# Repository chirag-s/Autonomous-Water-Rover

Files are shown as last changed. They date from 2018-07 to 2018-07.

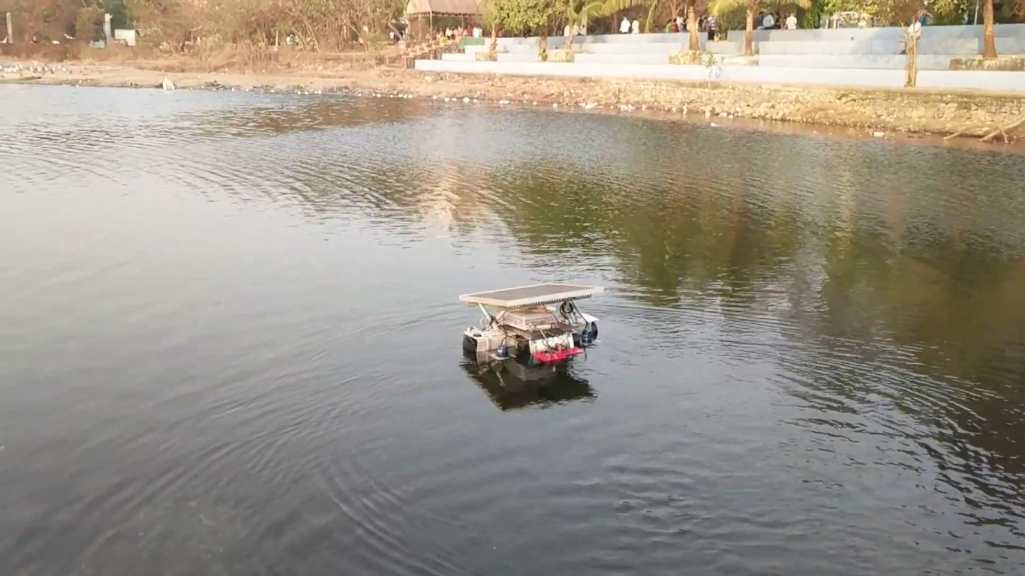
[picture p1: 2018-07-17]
Project Images/Project Testing/Mini Seasoe Testing manual.png

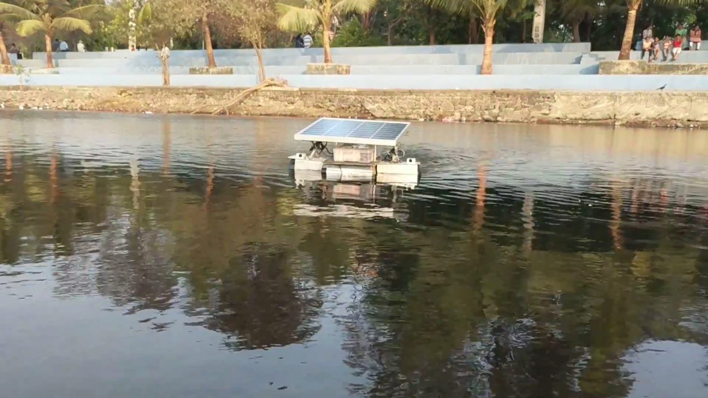
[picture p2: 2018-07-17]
Project Images/Project Testing/Mini seashore testing .png

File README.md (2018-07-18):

# Autonomous-Water-Rover

Water pollution is an age-old problem. Effective technologies and regulations to counter this is still under research with a booming rate. However, to solve a problem, identification and localization of the root source is essential. Today, to recognize the lakes or any other water bodies not satisfying the safety regulation, manual methods are employed. Stationary ground stations with sensors immersed at fixed points are used to measure the water parameters.

The Autonomous Water Rover monitors a water body by following the path specified by the user using GPS coordinates and traverses the water body as per the instructions with obstacle avoidance. It has different sensors like pH, percentage of dissolved oxygen, temperature, turbidity, etc. which gives us real time data on our server about the different parameters of the water body. A sonar transducer is also used to provide depth information up to 100 feet. The depth information of a water body can be used by ports, dredging companies and hydrographic offices. The rover also has a camera with first person view which can stream live video to a website in case of any emergencies regarding the waters or on rover itself. An AWR is really helpful as it will autonomously do some specified tasks which at present are carried out by humans.

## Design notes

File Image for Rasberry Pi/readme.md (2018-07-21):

The Configured Image for the Raspberry Pi is available on the below link :-

https://drive.google.com/file/d/1N4698NO5Q2EfMxIUc71g-TSj_-oGwf1t/view?usp=sharing

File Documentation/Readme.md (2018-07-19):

AWR Circuit Diagram
--|Contains the schematic used for motor driver, power distribution and arduino pro mini shield

Circuit Image
--|Shows the assembled circuit to give a gist regarding the wiring

Final Thesis Submission
--|Explains the entire project in great detail

Hardware Setup Guide
--|Explains the system components and the circuit diagram

Mechanical Setup Guide
--|Explains the mechanical assembly in DIY format

Process Flow
--|It expalins the steps the user has to follow with an Autonomous Water Rover to make it work through a flow chart
Software Setup Guide
--|Explains the software requirements and useful links to debug errors while setting up this project.
--|The codes folder in the repository has the entire file structure and its explanation.

Under Water Image Processing
--|It contains the explanation to the processing done, for under water images captured using a GoPro

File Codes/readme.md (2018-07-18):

File Structure

Arduino RC to PWM
--> Code to be uploaded on arduino used for reading Rc outputs from navio 2

Arduino Pro Mini
--> Code to be uploaded on arduino used for reading sensor data

SensorLog.py
--> Code to be executed on Raspberry pi having navio2 to get data from arduino having sensors

sensorsData.db
--> Sqlite3 database having two tables
----|GPS Data
-------> Table having only 1 row and is updated by GPS.py in folder WebServer. It stores the lat-lon values along with fix status
----|Sensor Data
-------> Table having sensor data and timestamp

WebServer
--|app.py
----> Execute to start web server
--|static
----> Contains all media, CSS and JS libraries
--|templates
----> Contains all HTML layouts
--| navio
----> Contains libraries necessary in app.py to send RC outputs

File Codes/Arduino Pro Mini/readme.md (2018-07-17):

This file is used for arduino which is used to get sensor data aand send it to RPi

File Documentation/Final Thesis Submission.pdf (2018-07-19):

Chapter 1: Introduction

This chapter presents the motivation for undertaking this project. It also emphasises the

need of water quality monitoring and our objectives.

### 1.1 Motivation

At present, in India, lakes and wetlands are in varying degrees of environmental

degradation due to industrial pollution. Despite knowing their environmental, social and

economic significance, city planners have neglected these water bodies. Today these

water bodies are at a high risk due to sewage and garbage disposal.

Pollution in large water bodies has resulted in a lot of disasters affecting aquatic life and

the complete biocoenosis. Carcasses of aquatic animals are washed off shore due to

mixing of pollutants, oil spills, etc. Thus, we felt a need to monitor the health of such

large water bodies, using sensors and GPS control, in order to maintain balance in the

ecosystem.

After a discussion about our project with an Indian Navy officer at INMEX SMM 2017

we realised about the problems faced by port authorities, to maintain channel depth to

prevent grounding of ships. In most ports, channel depth is identified separately by a

coast guard. However, this can be done by a rover which can use SONAR and model the

underwater bed of waterways so that we can keep a track and maintain a pathway for

boats.

Flooding of cities and villages happens due to various reasons. On 29th August, 2017

Mumbai was flooded. In the aftermath, it came to light that a doctor lost his life because

of an open manhole. We believe that in the aftermath of floods, our autonomous rover

will be capable of detecting such manholes via SONAR and pave a road where it is safe

to walk. Also, emergency supplies like medical aid/food can also be delivered to stranded

people at required locations using the rover by rescue officials.

After speaking to scientists at National Institute of Oceanography, Goa we understood

that underwater imaging is required to study the geological features of the coast.

Traditional surveillance boats cannot be operated in these shallow waters hence the

Autonomous Water Rover can be used to get underwater images in these regions.

The following articles published in leading newspapers emphasize on the water quality

problems observed in India :

Fig. 1.1 Water Pollution in 2018 | Fig. 1.2 Water Pollution in 2016

From above two articles it can be seen that the pollution in Powai lake has increased 1.6

times in just two years and if active measures are not taken to curb pollution it will likely

increase in the coming years.

### 1.2 Objective

The Autonomous Water Rover (AWR) is aimed to be an unmanned surface vehicle that is capable of traversing water bodies in remote controlled or in autonomous mode.

The AWSR is aimed to be developed as a novel marine monitoring and surveillance technology that can continuously collect data on water quality in lakes, rivers, channels, ports and estuaries. The water parameters targeted are pH, temperature, turbidity, salinity and depth. The list of parameters were finalised after interaction with scientists from Naval Materials Research Laboratory and National Institute of Oceanography.

The AWSR will traverse a water body by following the path specified by the user using GPS coordinates along with active obstacle avoidance. It will also have a manual mode accessible through a website.

It will have surveillance equipment in the form of waterproof camera for underwater imaging, a sonar which will illustrate depth contours, fish targets and other structures. These features are of utmost importance for defence and hydrography purposes.

Our aim to track pollution by using Autonomous Water Rover will take the aquatic surveying industry closer to industry 4.0 by incorporating Internet of Things, Robotics and Cloud Computing along other cutting edge technologies. The next chapter summarises research done on unmanned surface vessels for various applications.

Chapter 2: Literature Survey

This chapter presents the overview of the technological research and advancements and the comparative study of various USV technologies and products available commercially along with their applications in research and bathymetry studies.

Papers from 1994 are taken into consideration for this project. Some of the papers were

used to understand autonomous vehicles and their functioning along with applications,

while some were on combined works in all the 3 fields. The research work on all the

fields mentioned above is given below.

### 2.1 Autonomous water vehicles and applications

Exploring water bodies using manned and unmanned vehicles dates back to post WWII.

Since then many developments have been made, which can be broadly classified as

Remote-controlled vehicles and autonomous vehicles.

Some papers have aimed at collecting data from bottom transecting vehicles (ROVER)

[1], while some provide robust designs for research in cooperative autonomy [2]. Rest of

the papers focused on developing different methodology for achieving specified targeted

goals.

Sr. No. | Category | Author(s) | Year
1 | Unmanned Surface Vehicles [3] | Justin E. Manley | 2008
2 | Research | J. Curcio, J. Leonard, A. Patrikalakis | 2014
| | Erion Plaku, James McMahon | 2016
| | Geoffrey A. Hollinger, Urbashi Mitra, and Gaurav S. Sukhatme | 2012
3 | Other Applications | Inspection | Pere Ridao, Marc Carreras, David Ribas, and Rafael Garcia | 2010

| Brian Bingham, Brendan Foley, Hanumant Singh, and Richard Camilli | 2010
| Thomas Birtchnella & Chris Gibsona | 2015
Defense | Thomas Pastore, Vladimir Djapic [4] | 2010
| P.E Hagen, N Storkersen | 2003
| Liam Paull, Sajad Saeedi, Mae Seto | 2012
| E Bovio, D. Cecchi, F. Baralli | 2006

Table 2.1 : List of papers based on applications

### 2.2 Combined study

While few researchers were studying about aquatic life, developments were made

simultaneously in existing models by other engineers and researchers, which involved

combining concepts of machine vision, AI or IP or by satellite control. Their research

works are listed in the table below.

Sr. No. | Category | Author(s) | Year | Specification
1 | Surface Monitorin g and sampling | Goudey, T Consi J. Manley, MGraham | 1998 | Fish Monitoring
| | Caccia M, Bono R, Bruzzone Ga | 2005 | Sea Surface sampling
| | J.E Manley | 1997 | Surface robot
| | J. E. Manley, A. Marsh, W. Cornforth | 2000 | Surface craft
| | Iuliu Vasilescu, Keith Kotay | 2005 | Data collection
| | Matthew Dunbabin, Alistair Grinham, James Udy | 2009 | Surface monitoring

2 | Fish Monitorin g | M Dunbabin, L Marques | 2012 | Monitoring
| | P. Newman | 2002 | Operating Suite
| | J. Vaganay, J. Leonard, J. Curcio, and S. Willcox | 2004 | Navigation
| | Elgar Desa, R. Madhan and P. Maurya | 2006 | Ocean Data
| | Yun-Heh Chen-Burger , Gayathri Nadarajan, Robert B. Fisher | 1995 | Tracking Fish
3 | Depth and bed surface monitorin g | T Vaneck, M Schmidt | 1996 | Bathymetry
| | L. L. Whitcomb, D. R. Yoerger, and H. Singh | 1999 | Navigation of underwater vehicle
| | C.C. Eriksen, (http://ieeexplore.ieee.org/search/searchresult.jsp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) T.J. Osse, (http://ieeexplore.ieee.org/search/searchresult.jsp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) R.D. Light (http://ieeexplore.ieee.org/search/searchresult.jsp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) | 2001 | Depth monitoring and research

Table 2.2 : List of papers based on combined applications

### 2.3 RESEARCH GAP

In all, 23 research papers were studied. These papers were categorized according to the

categories mentioned above. Above literature review shows that studies are going on

simultaneously on autonomous water vehicles as well as their advancement. Thus,

selecting a proper research gap has become an important in this case. A small summary

was made in order to identify the research gap as shown below.

### 2.3.1 Area of Research

In this section, all the papers are broadly classified as per the major area of research.

Main | categories | are: | Research, | Monitoring | and | Defense.

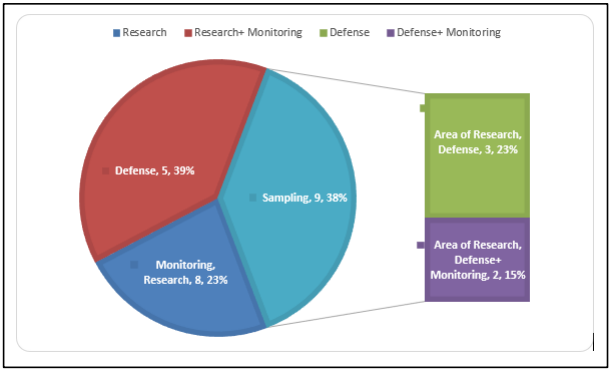
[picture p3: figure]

Fig 2.1 Application based categorisation of literature

From the above chart, it is clear that till date, surface water vehicles are used for data

acquisition mostly targeted on water beds. Least research is in field of dredging and

surface quality monitoring. Hence these field are chosen.

### 2.3.2 Year of Research

Fig

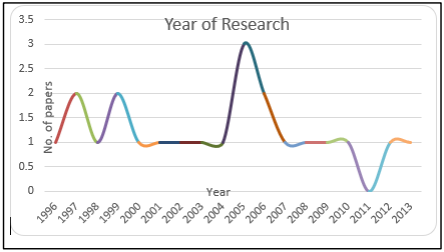
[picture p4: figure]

2.2 Categorisation of literature with time

The above chart shows that research is continuously going on from year 2010 in these

fields. Thus, there is no saturation in our area of research and there is continuous

development in this stream.

### 2.4 A review on water quality mapping in Powai lake

The paper ―Water Quality in Powai Lake, J.G Kiloyar, N.S Rokade, Taal2007: presented

at the 12th World Lake Conference, 2008‖ discusses the water quality of Powai lake

which is a large artificial lake, situated in a northern suburb of Mumbai. The purpose of

this paper, in this survey is to collect information concerning use and value of water

quality monitoring at Powai lake that might affect aquatic life. This paper studies the

changes in different parameters of water as the season changes. For this, it maps the

presence of impurities in the lake and many different parameters like DO, COD,

Nitrogen, TDS, COnducting, Salinity, Chloride, Total Hardness, pH and Alkalinity.

It was observed that during the month wise sampling of the various physio-chemical

parameters of the lake, the samples collected were position specific. However, the

process of collecting the sample was manual and the positional accuracy might have varied over the months. Also, a more precise and accurate data variation can be structured

if the number of samples obtained are more.

The graphs below show the variations of conductivity and pH as measured every month

at six stations over a period of six months.

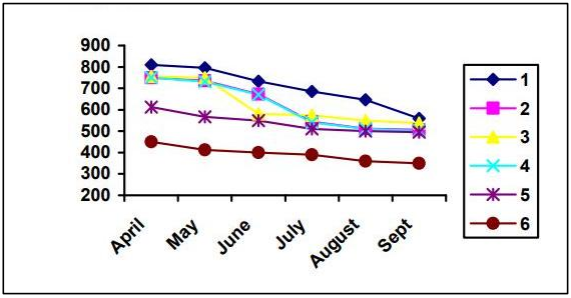
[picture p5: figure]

Fig 2.3 Variation of conductivity with time and location

Fig 2.4 Variation of pH with time and location

### 2.5 Commercially available Unmanned Surface Vehicles

Commercial products were also studied to analyse the existing technologies and the

capital associated to address these problems.

Kongsberg Gruppen located in Norway, has developed GeoSwath 4R USV, for bathymetry and hydrography surveying. It is capable of :
- Ultra high resolution wide swath bathymetry (FOV 240 - degrees)
- Geo-referenced side scan
- Radio control up to a range of 2 km
- Enduring 2.5 hours of continuous operation

Oceanalpha Company Limited located in Guangdong, China has developed ESM30 USV, for water quality monitoring and sampling. It is capable of :

- Measuring parameters such as pH, DO, temperature, ORP, conductivity and turbidity.
- Sampling water at four locations for further analysis in labs.
- Autonomous navigation, remote operation along with obstacle avoidance.
- Video streaming upto 2 km and data communication upto 5 km
- Enduring 3.5 hours of continuous operation
- Cost $52,000/-

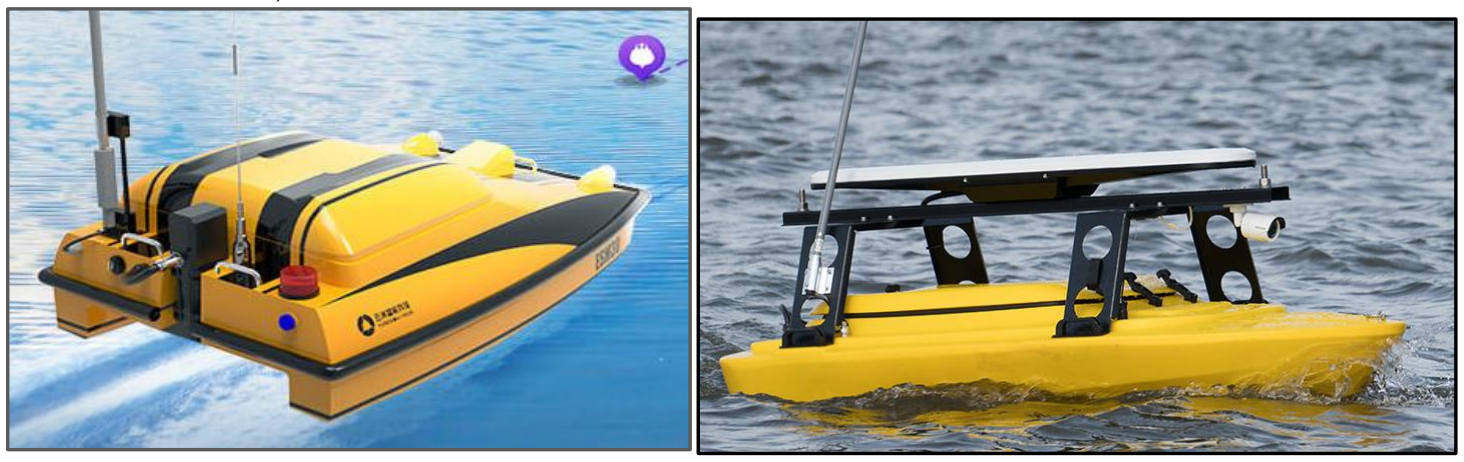
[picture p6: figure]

Fig 2.5 GeoSwath 4R USV | Fig 2.6 ESM30 USV

After going through the ongoing research and development in the field of unmanned

surface vessels, the design and development of Autonomous Water Rover will be

explained in the next chapter.

Chapter 3: Project Design

### 3.1 Design Considerations

The requirement of the surface vehicle with the targeted objectives was the first

consideration for selecting the base of the rover. The rover is required to provide

maximum payload capacity in minimum volume. There should be a container inside or

on the rover which can contain the electronic components for the entire rover. The

compartment must be waterproof and must prevent water from entering the container.

Also while providing with waterproofing the compartment should also not interfere with

any signals that is being transmitted or received by the transceivers inside the

compartment like GPS and compass. A camera is required for first person view of the

rover which should have sufficient field of vision to cover the entire forward path. In

addition the rover should also feature a propulsion system to drive the rover and a

maneuvering system for controlling the heading direction. Additionally, to increase the

mission duration of the rover, it should be provided with a secondary power source

preferably solar power.

### 3.2 Support Structure

3.2.1 Hull selection

After considering our application it became evident that speed was not of great

importance for our use and emphasis was given to simplify the manufacturing process

and keep our project cost-effective. Most boats feature a hull made of aluminium, while

most of the unmanned vehicles tend to feature fiber reinforced polymers. Analysis for

selection of the material of the rover‘s hull was done with feasibility and time as the

major decisive parameters.

Hull material options:

Metal: Most rovers and made with metal hulls. They generally fall in two

categories: Aluminium and Steel. Metal hulls provide high strength and more impact

damage resistance. Relative to their weight, aluminium provide incredible strength and

are highly ductile. The pitfall with metal hulls in water rovers are their vulnerability to

corrosion, scaling and providing shielding effect for components placed inside the hull.

The aluminium hulls are also prone to galvanic corrosion with a stainless steel propeller

or bolts. The outside of the hull are prone to rusting and pitting due to this galvanic

corrosion.

Wood: Wood is another known material which is known to be used for building

boats for a very long time. Wood has less density than water so it floats giving high

buoyancy posing as a safe and sturdy vessel. However, using wood as hull also has some

drawbacks. If left in water for long time, worms eat away the timber. Termites attack the

dry wood. SInce the rover is meant to be used to still waters marine bores poses as a great

threat to the hull. Wood hulls are susceptible to to electrolysis damage. Electrolysis can

cause damage to the to the wood and turn them into mulch and mush.

Fiberglass: Fiberglass reinforced plastics is the most widely used hull material in

unmanned surface as well as underwater vehicles. FIberglass provide thinner hulls with

comparable strength. Thinner hulls do then to flex more and can be given any desired shape. Fiberglass vessels also tend to be lighter and provide sufficient strength for long

lasting structures. Fiberglass are invulnerable to any kind of electrolytic damage or

corrosion. At first glance it seems like fiberglass can be the best available material for the

hull of the rover. The only constraint with it is the availability and the capital required for

its manufacturing.

After examining the available materials and resources we decided to use PVC pipes for

the the support structure for our AWR. The overall benefit of using PVC pipes are:

improved stability, increase in the load capacity and reduction in manufacturing cost.

PVC pipes were used for the following reasons :

- They are manufactured to transport liquids (mostly water); for this they are

manufactured so as to sustain high pressure. The water at the surface of water

bodies exert significantly lesser pressure, making our rover apparently leak

proof.

- Sealing the ends of the pipe is possible as standard end caps are available.
- Multiple pipes can be attached according to the requirement of length and

width in accordance with maximum roll and pitch the rover needs to sustain.

- Impervious to attack from fungi.

While PVC pipes exhibit high resistance to abrasion, they are affected by the

environment. The following are the effects of varying environmental features on the PVC

pipes:

Thermal Effects:

The properties of the PVC pipes are significantly related to the operating

temperatures. The rover must be deployable in wide varieties of water bodies with

varying temperatures. Also the temperature significantly varies throughout the day in a

single water body. PVC pipes are rated for maximum performance at 23°C; as the

operating temperature decreases, the pipe‘s stiffness and the tensile strength increase,

thereby increasing the pipe‘s pressure capacity.

Biological Attack:

PVC pipes are nearly impervious to biological effects. These attacks can be

caused by the action of living microorganisms viz. Bacteria and fungi. PVC pipes will not

deteriorate or break down under such attack, nor will it serve as a nutrient to

microorganisms, or fungi.

Weathering Resistance:

PVC pipes can incur surface damage when subjected to long exposure to

ultraviolet radiation from sunlight. While the rover is supposed to work in direct sunlight

it became imperative to rule out the vulnerability. This was achieved by physical coating

of the pipes with layers of oil paint. Since the ultraviolet degradation occurs when energy

from UV rays leads to excitation of the molecular bonds in the plastic, the layer of paint

prevents any direct contact between the PVC and sunlight.

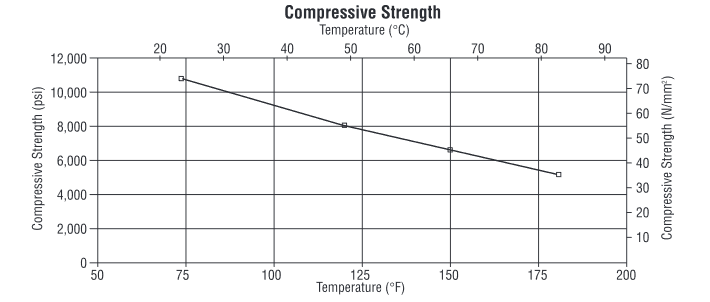
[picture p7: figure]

Fig 3.1 Compressive strength graph for PVC

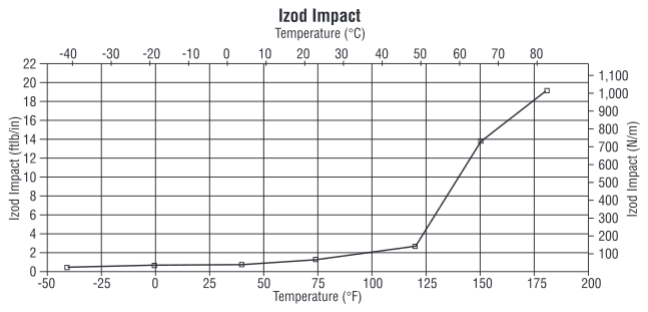
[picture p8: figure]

Fig 3.2 Izod Impact test graph for PVC

### 3.3 Boat Structure:

The primary requirement of the support structure of the rover is to provide stability,

buoyancy and a solid platform. Owing to the limited manufacturability of the PVC pipes,

we selected the conventional raft type structure.

We selected PVC pipes of varying lengths with outer diameter 16 cm and coupled them

together representing a raft for making the support structure of the rover. The middle pipe

was kept the longest and one small pipe was attached on front and back each. This

provided with maximum roll stability while keeping the weight minimum.

The total number of pipes to be joined was decided as per the payload of the rover. The

layer was made by adding 3 pipes of lengths 300 mm, 300 mm and 900 mm.

The three pipes are held together in place using a aluminium strip loop wound around

them. The Al strip is kept in tension to retain its shape and an adhesive is used to close

the loop while retaining it on the pipe. Additionally copper wires were used to increase

the tension in the strip to ensure firm structure of the support.

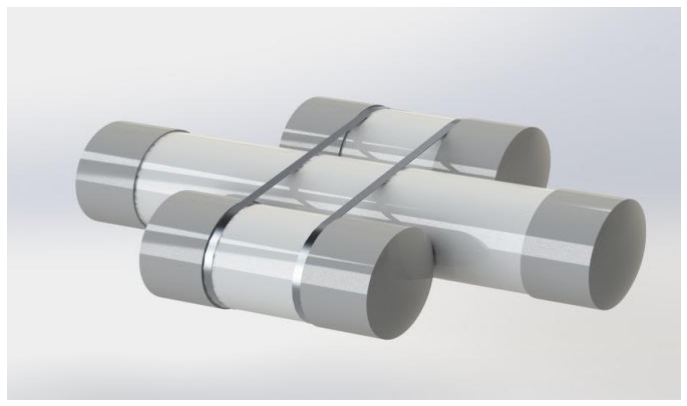
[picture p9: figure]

Fig 3.3 Support Structure

### 3.4 Buoyancy calculation:

Buoyancy = Weight of fluid displaced

Buoyant force is given by:

Volume of pipes :

The total weight of fluid displaced is about 30.56 kg.

### 3.5 Top Plate: The PVC pipes provides round surface which cannot be used for any kind

of mountings. Furthermore to secure waterproofing it was opted to avoid any kind of

drilling in the pipes. So a 2 mm aluminium sheet was used as the top plate to provide a

constant surface. This allowed all the components, equipments and thrusters to be

mounted on the rover with additional reinforcements.

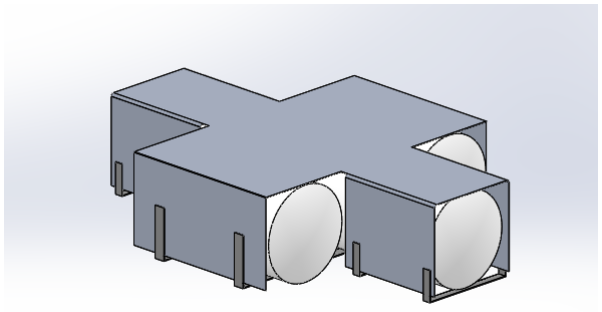
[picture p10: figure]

Fig 3.4 Reinforcements

### 3.6 Propulsion System:

Motor Selection:

The target waters for AWR are still and weedy waters. Conventional propulsion

system has a potential to clog in weeds and needs to be cleared. Instead it was decided to

use differential reaction drive for propulsion using two submersible pumps.

The reaction drive works by having an intake which is located below the hull submerged

in water. Water enters the pump through the inlet. The pump is usually centrifugal pump

for higher speeds or axial flow type for medium or low speeds. The water pressure in

increased inside the pump and is directed outward through a nozzle.

### 3.7 Thrust Calculation:

Thrust from a propeller is given substituting Bernoulli‘s equation into thrust equation

(momentum equation)

Substituting in Bernoulli‘s equation:

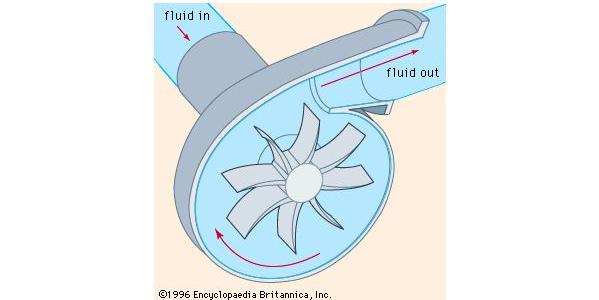
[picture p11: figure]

Fig 3.5 Working of Bilge Pump

The pump selected was Vetus V1000.

The bilge pump exhibits the following superiorities which made it most viable propulsion

system for our rover:

- The bilge pumps are submersible water pumps. So there was no need of

waterproofing the motors.

- Since the impeller is directly attached to the motor shaft in the pump there was no

need for transmission shaft.

- The pumps can be directly mounted outside and there‘s no need to locate them

inside the rover body.

- A filter is provided to prevent seaweed from getting stuck in the impeller.
- Speed can be adjusted by controlling the rotation speed of the motor.

### 3.8 Final Design:

Fig 3.7 CAD of Final Design

The final design includes a polypropylene sheet on top of the aluminium sheet for

insulation from circuits. A solar panel is added to recharge the battery and add to the run

time of the rover.

Principal axes of inertia and principal moments of inertia: ( grams * square millimeters )

Taken at the center of mass.

Ix = ( 0.00, 0.00, 1.00) | Px = 897234608.07
Iy = ( 0.96, 0.27, 0.00) | Py = 1136627042.03
Iz = (-0.27, 0.96, 0.00) | Pz = 1291193297.90

Center of mass: ( millimeters )

X = 2.38

Y = 171.37

Z = 349.05

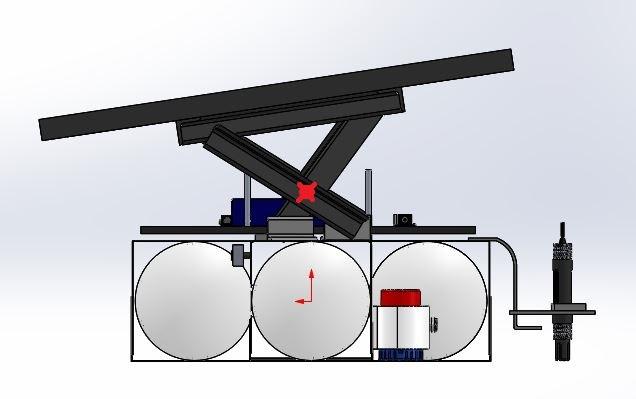
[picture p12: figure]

Fig 3.8 Center of mass position (Side View)

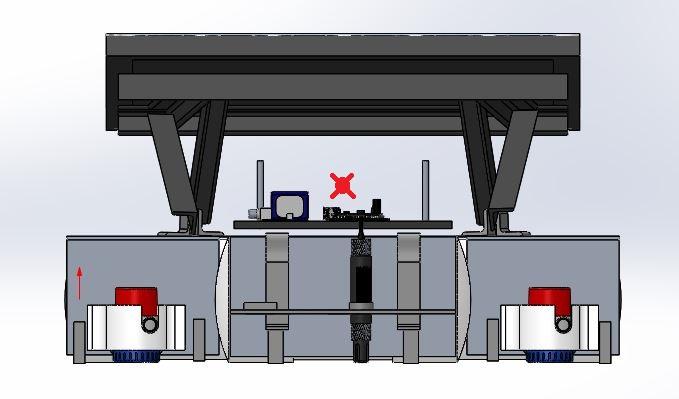
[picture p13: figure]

Fig 3.9 Center of mass position (Rear View)

Chapter 4 : Implementation Details

This chapter presents the hardware design, software implementation, cost report and

testing results for the various components of the Autonomous Water Rover. It also

presents the image processing algorithm used for enhancement of underwater video feed.

### 4.1 System design

The figure below illustrates the various components in the Autonomous Water Rover and

their relation with one another. Some of the components like the thrusters and the solar

panel were explained in the product design section. The hardware and software

components will be covered in this chapter.

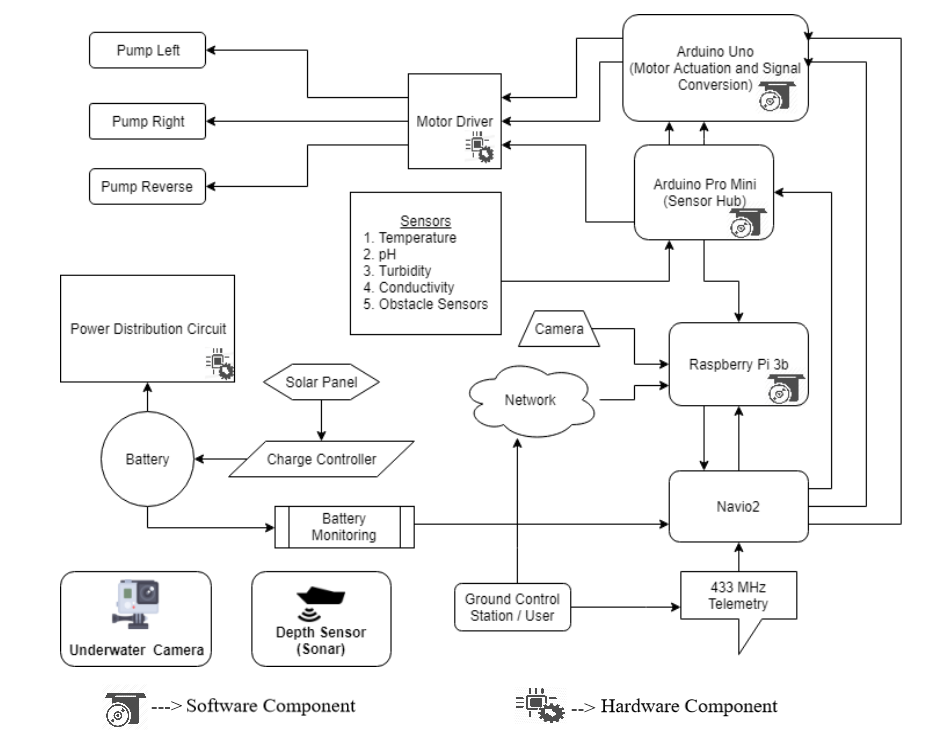
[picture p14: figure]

Fig 4.1 System Design

The various components in the above figure are as follows :-

- Power System: The power generation, storage and distribution includes the

following main components :

- Battery : LiPo will be used to ensure operation of rover for over an hour

on one charging

- Solar Panel : A 50W Solar Panel is used to charge the 12 volt battery and

also increase the operation period

- Charge Controller : A 20A 12V waterproof solar panel charge controller

will be used

- Voltage regulation : Voltage regulators will be used to always keep the

supply voltage for the pumps constant i.e. 12V to obtain similar

performance even at different battery levels. Also 5V and 3.3V voltage

regulators will be used for obtaining required supply voltage for the Rpi

controller board, Navio2, telemetry and all installed sensors on the rover

- Raspberry Pi 3b : It is a single board computer which will be used for complex

path planning through ardupilot, hosting the web interface, providing live video

streaming and communicating with sensor nodes

- Navio2 : It is an autopilot Hat for Raspberry Pi 3b which simplifies autonomous

navigation by bringing multiple sensors on a single board and by seamless

integration with Raspberry Pi. It also has analog to digital converters along with

pulse generators to produce pulses which can control servo motors. The following

sensors will be used by the Autonomous Water Surveillance Rover :

- GNSS Receiver : Tracks GPS, GLONASS, Beidou, Galileo and SBAS

satellites for accurate positioning

- Dual IMU : Accelerometers, gyroscope and magnetometer readings will

be used for orientation and motion sensing

- High resolution barometer : Senses altitude with 10 cm resolution and can

be used to relay accurate location information along with GPS

- Communication Ports : UART interface will be used to relay information

through telemetry radio

- Ground Control Station : It could be any windows based personal computer

having Mission Planner installed

- Local Area Network : A LAN is created to access the website hosted on the

raspberry pi. It is not needed for operation in autonomous mode

- | Telemetry Radio : The | mRo SiK Telemetry Radio V2 operates at 433Mhz and

provides 300m range by default. This radio will be the link to relay localization

details and program missions for the rover remotely

- Underwater Camera : A GoPro hero is used to gather images of the underwater

bed upto three meters. As penetration of light at this depth is sufficient, an

illuminating light source will not be necessary. The light source can be fitted to

the base of the rover for illumination if surveillance is to be done in the absence of

| sunlight
- Camera : A raspberry pi camera version 2 is used to provide live first person

view of the rover to operator

- Sensor Node : Data acquisition from the environment will carried out and the

information will be relayed to the Rpi. An arduino pro mini is used because of its

small form factor for interfacing the sensors and communicating with raspberry pi

- Distance Sensors : Two waterproof ultrasound (40 KHz) distance sensors i.e.

JSN-SR04T are used to detect obstacles on the surface of the water and in the

| forward path of the rover
- Water Quality Monitoring Sensors : To measure the quality of water following

parameters are being measured :-

- pH : DFRobot Gravity : analog pH sensor is being used to measure the pH

of water. The pH measurements have a resolution of ± 0.1pH at 25 ℃

- Temperature : DS18B20 waterproof temperature sensor probe is used to

get ±0.5°C accuracy in the range -10°C to +85°C. It uses 1-Wire interface

i.e. requires only one digital pin for communication

- Conductivity : A generic rain sensitive sensor module is used in analog

mode to get the conductivity readings. The accuracy of this module for

measuring isn‘t high but can be used for thresholding purposes

- Turbidity : DFRobot Gravity : analog turbidity sensor is used to obtain the

turbidity readings which is later converted to NTU units.

- Fish Finder : ZEEPIN Fish Finder is a wireless & rechargeable sonar sensor

along with a smart portable LCD display which is used to get depth data,

temperature data along with the add on of identifying fishing areas

- Signal Converter : The output signal from the Navio 2 is in the form of RC

pulses of the duration 1ms to 2ms. The external interrupt pins of an arduino uno is

used to measure the pulse widths of these pulses and accordingly generate a PWM

signal which drives the motor driver circuit

- Motor Driver Circuit : The arduino uno will send control signals to the motor

driver which in turn will control the actuator i.e. pumps. The pumps will be

operated at variable speed according to navigation control using PWM to allow

more precise control over the rover

### 4.2 Hardware Design

Hardware design has three main components. They involve the power distribution circuit,

the motor driver circuit and other peripheral device connections. A circuit as shown

below was designed to reduce wire connections and also to simplify sensor interfacing. It

includes the power distribution system, the motor driver circuits and sensor input slots for

the Arduino Pro Mini.

### 4.2.1 Motor Driver Circuit

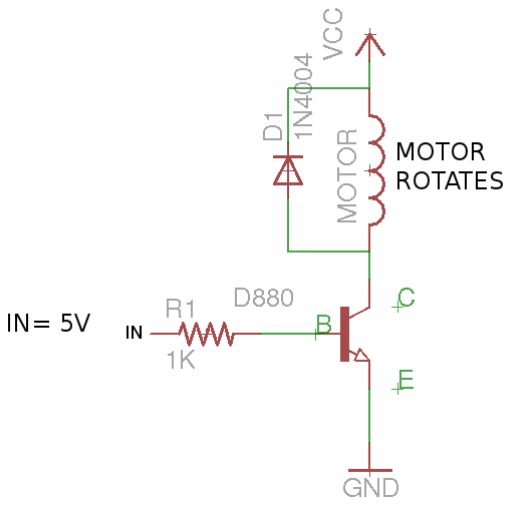
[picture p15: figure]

Fig 4.2 MOSFET schematic

Fig 4.2 shows the basic controlling of a motor using a MOSFET. We have used IRFZ544

MOSFETs to drive 3 bilge pumps. We did use standard motor driver circuits because the

pumps needed to be controlled in only one direction, unlike the standard motor usage

where we need bidirectional control. As the bilge pumps cannot propel water backwards,

we used 3 pumps, 2 at the back for differential propulsion and 1 at the front for braking.

To drive the MOSFETs, we need to control the voltage formed at the Gate w.r.t. Source

which is done by the Arduino Microcontroller. Proportionately, the Drain current will

flow through the bilge pump as required

### 4.2.2 Power Distribution Circuit

The 12V Lipo battery is connected to a General Purpose Board on which different

circuits of the system are soldered. The voltage is stepped down for powering the sensors

and the microcontroller board, using a LM2596 buck converter which step downs the

voltage from 12V to 5V. The circuit is soldered on a General Purpose Board.

### 4.2.2.1 Solar Panel

Calculations for Solar Panel and Battery

Operating Voltage of System =12V Current Consumption = 10AH

Power Consumption = 120W/hour

Per day power consumption = 360 WHr (Considering 3 trials per day)

Battery Ampere Hour Rating = 360W / 12V = 30A.

Battery of 12V 30A is needed

Charging time = 6 hours, 360/6 = 60Wh, 60/0.6 = 100W

Solar Panel of 12v 100W would be suitable for high efficiency

### 4.2.3 Peripheral Devices

The peripheral devices include the RPI 3b, Navio 2, Arduino Pro Mini, Arduino Uno and

sensors. The following subsection go through the process of

setting them up.

Attaching Navio2 to a Raspberry Pi

- Install spacers to the top side of Raspberry Pi and

fix them with screws from the bottom.

- Connect extension header to the 40-pin gpio port.
- Attach Navio2 to the extension header.
- Fix Navio2 using screws | Fig 4.3 Navio2 Setup

### 4.2.3.1 Making Wired Connections

After Navio2 is mounted on RPI we have to proceed and attach other peripherals and

wires for communication and sensors. The connection diagram is as follows :-

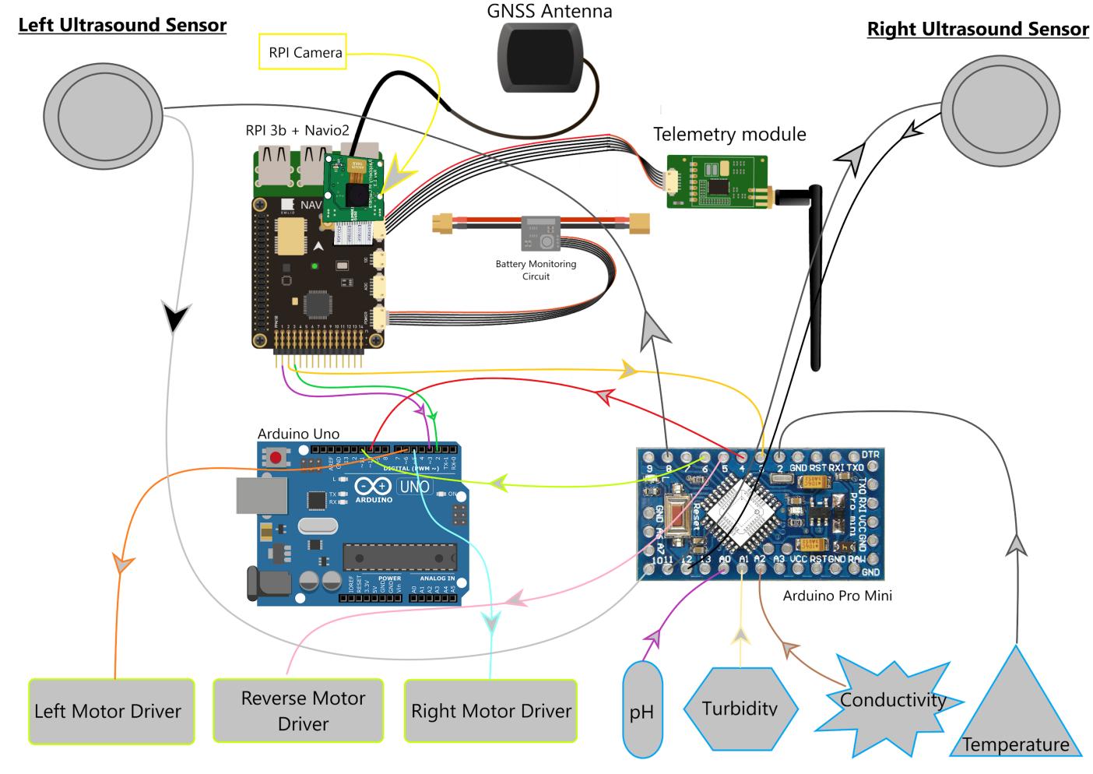
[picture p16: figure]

Fig 4.4 Peripheral Connection Diagram

In Fig 4.4 the power connections haven‘t been illustrated and are to be made for each

sensor. Each board also has a common ground connection. The Arduino Pro Mini is also

connected to the RPI through an UART to USB converter to communicate sensor data to

the RPI. At the Ground Control Station the receiver of the radio telemetry module is

connected using an USB connection. When the rover is to be deployed in manual mode a

local wifi network is created to control the rover from the web interface.

### 4.3 Software Implementation

As seen in Fig 4.1 there are three blocks which have a software component. They are :

I. Raspberry Pi 3B
II. | Arduino Pro Mini
III. | Arduino Uno

The three are related to one another as shown in Fig 4.1. The underlying technology stack

is explained in the following sections.

### 4.3.1 Raspberry Pi 3B

The RPI is used as autopilot with Navio2, as a server for the web interface and as central

hub for all sensor data.

- An open source preconfigured raspbian stretch image is provided by the

developers of Navio2. The image has the necessary drivers for communicating

with an ardupilot ground control station using MAVLink protocol. The image is

configured for an ardupilot rover during the initial setup. The calibration of IMU.

PID coefficients and other settings are configured using Mission Planner, which is

an open source Ground Control Station

- The web interface is hosted using a Flask application written in python. The

design of the website is done using HTML5 and CSS. Javascript is used for

dealing with dynamic page elements

- Major APIs used are Just Gauge for representation of sensor data and Google

Maps API for displaying real time location of the rover

- SQLite is used for storing sensor data received from Arduino Pro Mini and GPS

data from Navio2

- Matplotlib library in python is used for generating plots of sensor data which are

then displayed on the website

- Motion service is used on RPI to host live video stream on port 8080 of the RPI

which is also displayed on the website

- Socket programming is used in the flask server for updating the location of the

rover in real time.The screenshots of the various web pages are as follows :-

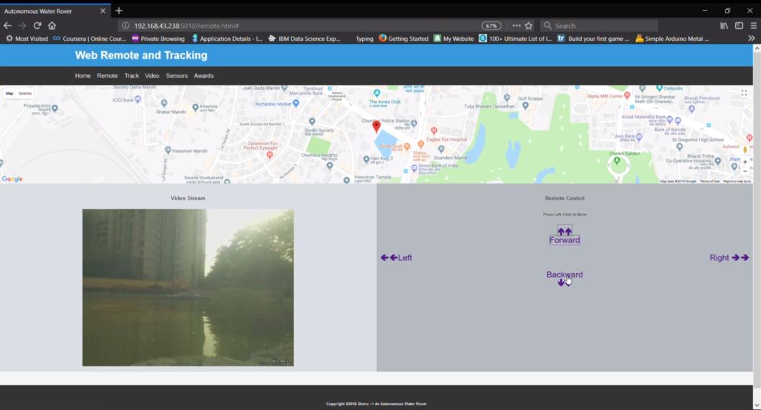
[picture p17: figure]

Fig 4.5 Remote Control Web Interface

Fig 4.6 Live Video Stream (First Person View of AWR)

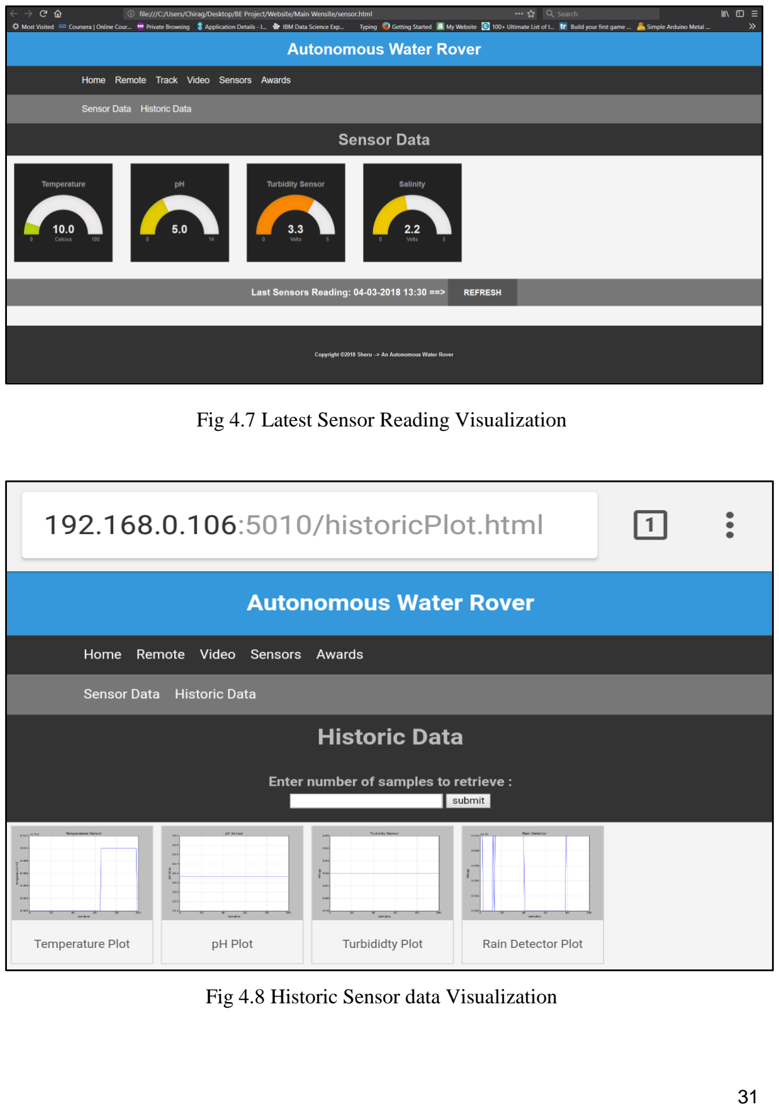
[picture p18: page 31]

Fig 4.7 Latest Sensor Reading Visualization

Fig 4.8 Historic Sensor data Visualization

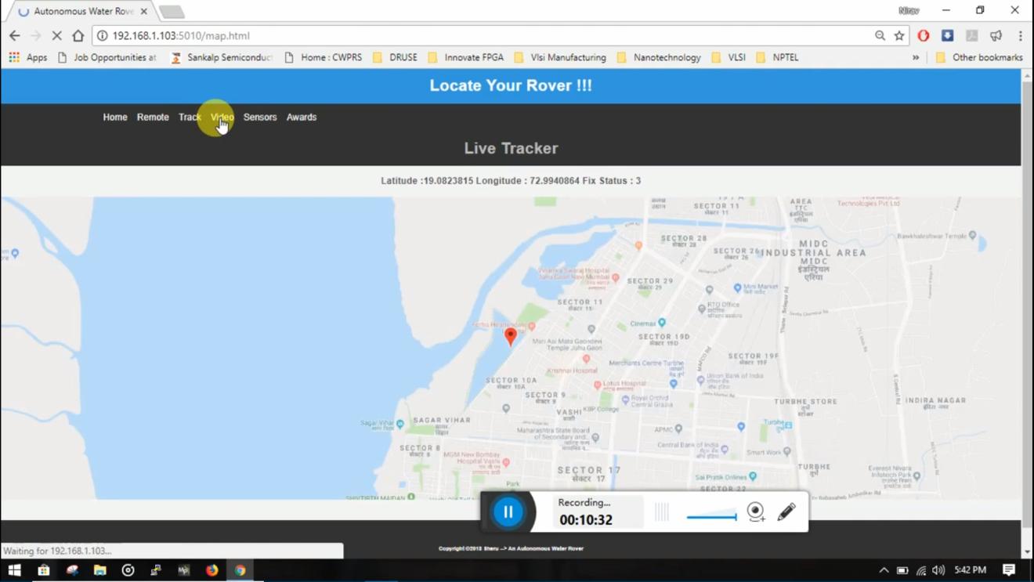
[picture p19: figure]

Fig 4.9 Location Tracker in the Web interface

### 4.3.2 Arduino Pro Mini

This device used as a sensor node which not only interprets sensor data but also does

some preprocessing and forwards the data to the RPI for further processing. The main

functions implemented on this device are :-

- Reading the digital values of the analog signals from pH, turbidity and

conductivity sensor through the ADC. Also, every final reading is the average of

40 readings in order to reduce outliers in sensor readings. The sensor reading is

then sent to the RPI as per the frequency decided by the user. One reading is

usually sent every eight seconds

- Temperature sensor readings are read by using the one wire protocol which is

implemented in the sensor

- Distance sensor readings are computed by triggering the sensors and then reading

the pulse width of the output signal at the echo pin of the sensor. After computing

the distance the sensors change the state of two digital pins which is then read by

the Arduino Uno to control the heading of the rover

- The external interrupt pin is used to measure the pulse width of the output signal

from tha Navio2 board. The pulse width is then used to compute the duty cycle of

the PWM signal which is given as input to the motor driver controlling the reverse

pump

### 4.3.3 Arduino Uno

This device is used as a signal converter as commercially available modules for the same

are expensive. The functions implemented on this board are :-

- It is used as a signal converter which measures the pulse width of pulses from the

Navio2 board using the external interrupt pins present on the microcontroller. The

pulse width is then used to compute the duty cycle of the PWM signals which are

given as input to the motor drivers controlling the right and left pumps

- It reads the state of two digital pins on the Arduino Pro Mini. These pins indicate

the presence of an obstacle if any, to the Arduino Uno

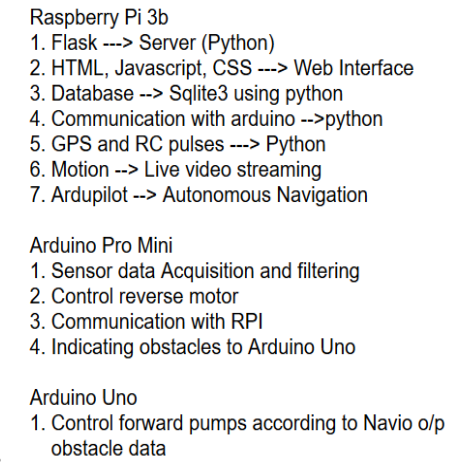
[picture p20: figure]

Fig 4.10 Tasks of controllers

### 4.4 Ground Control Station

Mission Planner a full-featured ground station application for the ArduPilot open source

autopilot project is used. It is compatible with Planes, Copters and Rovers but we are

using it in the Rover mode. It is compatible with Windows only. Mission Planner can be

used as a configuration utility or as a dynamic control supplement for an autonomous

vehicle. Few actions that can be accomplished using Mission Planner are :-

- Load the firmware on the Navio2 board
- Setup, configure, and tune the AWR for optimum performance
- Plan, save and load autonomous missions into the autopilot with simple point-

and-click way-point entry on Google or other maps

- Download and analyze mission logs created by autopilot
- Interface with a PC flight simulator to create a full hardware-in-the-loop UAV

simulator

- With radio telemetry hardware we can :
- Monitor our vehicle‘s status while in operation
- Record telemetry logs which contain much more information the

the on-board autopilot logs

- View and analyze the telemetry logs

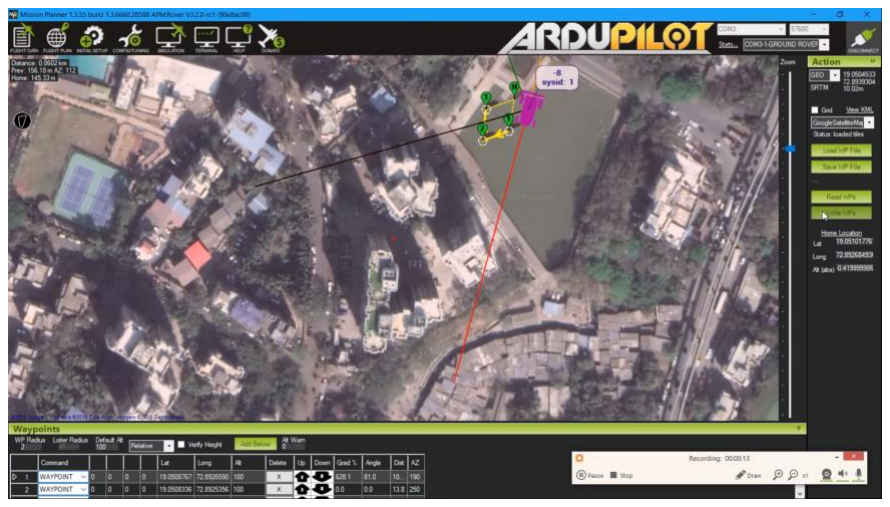
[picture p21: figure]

Fig 4.11 GCS waypoint Planning Interface

### 4.5 Under Water Image Processing using Wavelet Fusion

Taking reference from IEEE paper ―Underwater Image Enhancement by Wavelet Based Fusion‖ a model has been implemented to enhance an underwater video captured during the testing of ―Autonomous Water Rover‖.

The flow of the process is as follows :-
Step 1: Import image
Step 2: Contrast Adjustment using CLAHE
Step 3: Colour Correction using histogram stretching of V in HSV
Step 4: Wavelet Fusion of images from step 2 and 3 using
- 2 level decomposition
- A db2 wavelet
- ‗max‘ rule for approximate coefficients and ‗min‘ rule for detail coefficients
Step 5: Get enhanced image

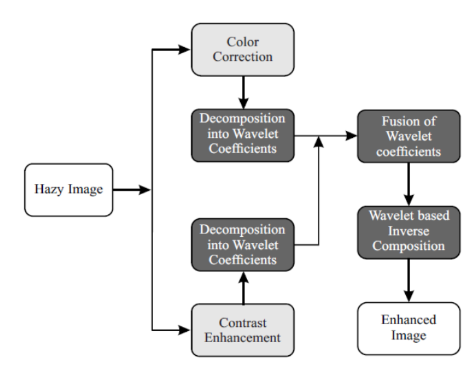
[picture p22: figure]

Fig 4.12 Underwater Image enhancement algorithm

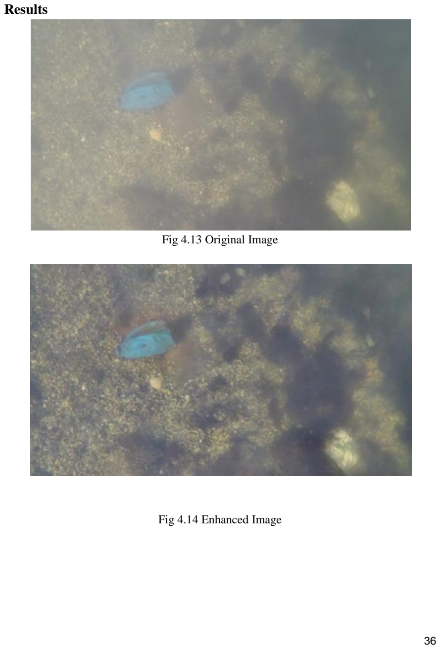
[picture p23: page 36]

Results

Fig 4.13 Original Image

Fig 4.14 Enhanced Image

### 4.6 Pricing Model

The prototyping cost of the model can be divided into two parts :

1. Autonomous Water Rover
2. Sensors for data acquisition

Table 4.1 : Retail Costing for Autonomous Water Rover

Sr. No. | Component | Price
1 | Mechanical Components | ₹6,500
2 | Hardware Components | ₹16,500
3 | Solar Panel and Circuitry | ₹3,500
| Total :- | ₹26,500

The above total cost of ₹ 26,500 is absolute for every user and is the base price to get a fully functional Autonomous Water Rover. As the rover can be used for various applications, depending on the application the sensors can be selected according to the need of the user.

We aim to build the model which is convenient for every use case .i.e. To provide the user the option to choose the sensors either from a list of sensors available or to enable him/her to incorporate their existing sensors onto the rover with minor modifications in the mechanical and software architecture of the AWSR.

Table 4.2 Retail Costing for Sensors on the AWSR:

Sr. No. | Sensor | Price
1 | Echosounder | ₹11,000 /-
2 | pH | ₹4,000 /-
3 | Turbidity | ₹1,500 /-
4 | Temperature | ₹165 /-

5 | Conductivity | ₹200 /-
6 | Underwater Imaging Camera | ₹30,000 /-

Hence, as per the needs of the user the user can customise the sensors needed for the mission.

### 4.7 Target Market

- AWSR can provide water quality data to the recipient government or non-government bodies for keeping a track on the fluctuations in water parameters viz. pH, temperature, salinity, dissolved oxygen.
- AWSR can also provide indigenous solution for fish tracking in freshwater bodies and in fish farming to aid fish dependent communities.
- In ports, the channel depth monitoring is essential for preventing grounding of ships. AWSR can be used to monitor the channel depths and provide seasonal data to dredging department.
- AWSR can assist the naval bodies by providing above water as well as underwater surveillance; while the rover is equipped with an echo sounder for depth mapping, it can also provide underwater video feed upto a depth of 5 m for hydrography mapping.
- AWSR can also aid the defence forces in emergency relief operations where emergency supplies are to be transported to stranded individuals in cases of floods and other natural calamities.

Chapter 5 : Implementation for deployment in real world

This chapter explains step by step procedure of working and also showcases the sensor

data accumulated

Step 1: Customising of the Rover

At this stage the user will have the flexibility to select the features of the water rover that the user needs to enable/disable. For instance in the application of surveying sea bed underwater camera, light source for flash, echosounder will be necessary.

Step 2: Deciding the Route of the Rover

The user will mark the checkpoints on a map with the order in which the areas have to traversed. This will be made possible by the computer application called mission planner for ardupilot compatible boards. A snapshot of the UI is as shown to right.

Fig 5.1 Mapping of checkpoints

Step 3: Programming the Rover

The user will program the ardupilot board i.e. the Navio2 mounted on the Raspberry Pi 3b through the mission planner software. Once the programming is done the rover can be deployed in the water body which has to be monitored. The point of deployment can be chosen according to the closest checkpoint.

Step 4 : Remote Control of the Rover

The user can give commands to the Rpi through the active telemetry radio which connects Ground Control Station and the Autonomous Water Surveillance Rover. New routes or evacuation signals can be sent through this link.

Step 5 : Data Acquisition and Visualization

The data gathered by the AWR is to the Ground Control Station and visualized using various data processing softwares such as R, python etc. This visualization will be made available to the user in real time, ensuring that time sensitive applications like emergency relief, surveillance and are not hindered.

Fig 5.2 Conductivity

Fig 5.3 Turbidity

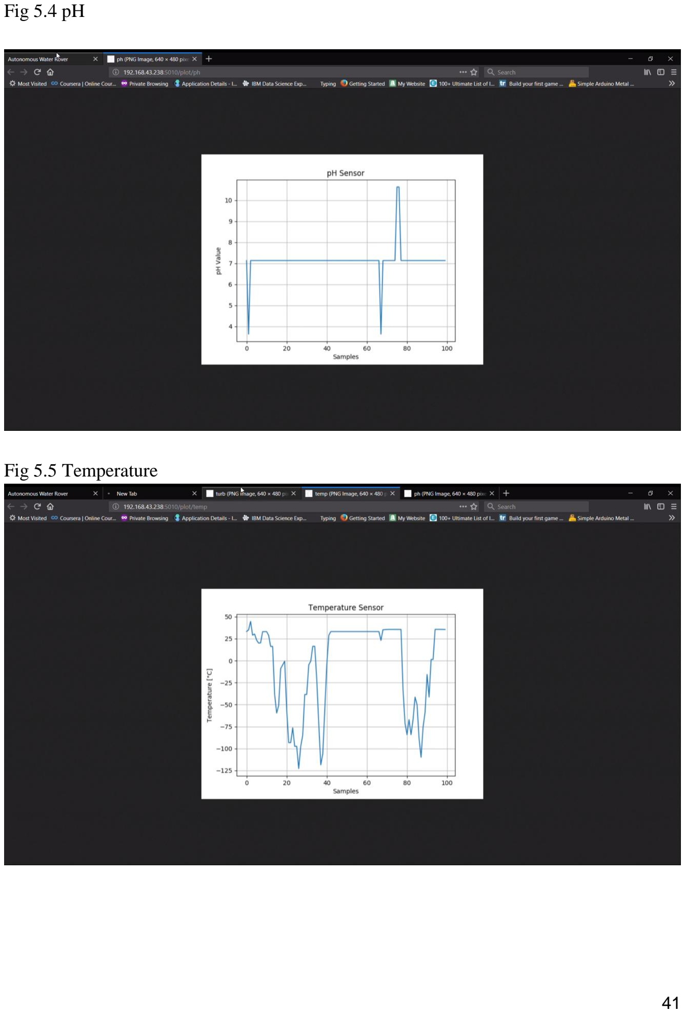
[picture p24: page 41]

Fig 5.4 pH

Fig 5.5 Temperature

Chapter 6 : Conclusion

This chapter explains our project’s capabilities and tells us the scope of

implementation in real scenarios

We tested our Autonomous Water Rover at multiple locations,first at Mini Seashore,

Vashi, Navi Mumbai, then at Teen Talav, Chembur and also at Neelkanth Housing

Society, Vidyavihar East for testing and modification purposes. While testing in the

swimming pool, we were assured of it‘s capability of traversing water bodies using

differential propulsion and manual control.

Autonomous mode of our rover was tested at Mini Seashore as the water pond was very

much similar to the conditions of a lake. Als0 the area was larger, GPS coordinates

assigned could be accurately interpreted by the rover. The sensors‘ data was collected and

displayed live on the dedicated webpage. Front and Underwater videos were displayed

live on the website and phone. SONAR accurately determined the depth of Mini

Seashore.

Targeted Users:

1. Municipal Corporations
2. Dredging Industry
3. Flood Disaster Relief

Teams

4. Fishing Industry

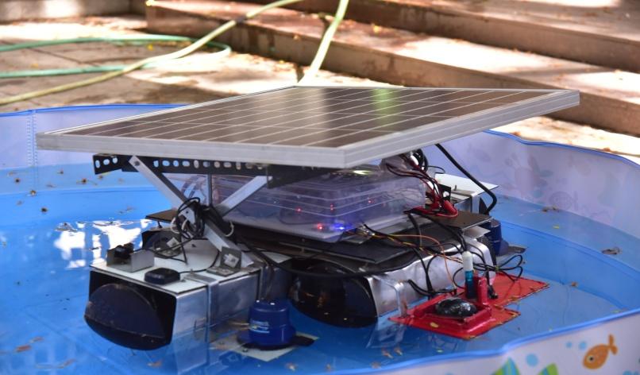
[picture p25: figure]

Fig 6.1 Autonomous Water Rover

Chapter 7 : Future Objectives

This chapter explains our project’s future undertaking and objective with respect to

multiple facets

We successfully built a prototype and achieved realistic results when tested in mini ponds

across Mumbai. As lakes are water sources for city needs and come under Municipal

Corporation & Forest Department‘s jurisdiction, we didn‘t get access to them for testing.

However, the ultimate goal is to implement such a Rover in lakes across the world for

continuous monitoring of lakes. From the technical perspective, following areas need

improvement:

1. Mechanical structure can be designed as a Catamaran structure for higher

mobility

2. More efficient design incorporating Solar Panel
3. Provide a simpler interface than website for controlling, for eg, mobile app
4. Electronics housing can be improved
5. Data Analytics for the monitoring the health of the water body

Apart from the improvements in the current prototype, different applications can be

achieved more precisely if the rover is an Underwater Autonomous Rover, like

1. Depth mapping using SONAR
2. Underwater survey using

Camera

3. Multiple defence applications

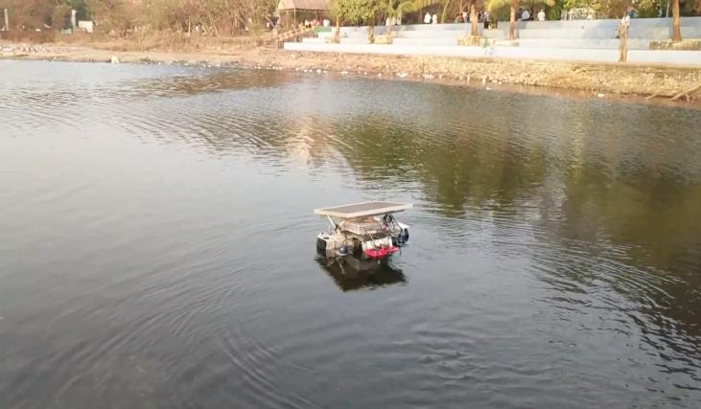
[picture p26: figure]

Fig 7.1 AWR in Mini Seashore

Bibiography

1. K. L. Smith, Jr. R. C. Glatts, An autonomous, bottom-transecting vehicle for making long time-series measurements of sediment community oxygen consumption to abyssal depths, American Society of Limnol, Oceanogr, 42(7),1997,1601-1612
2. J. Curcio, J. Leonard, A. Patrikalakis (2006), SCOUT - a low cost autonomous surface platform for research in cooperative autonomy, IEEE
3. Justin E. Manley (2008), Unmanned Surface Vehicles, 15 Years of Development, IEEE
4. Thomas Pastore and Vladimir Djapic (2010), Improving Autonomy and Control of Autonomous Surface Vehicles in Port Protection and Mine Countermeasure Scenarios, NATO Undersea Research Centre (NURC), 19126 La Spezia, Italy
5. Geoffrey A. Hollinger, Sunav Choudhary, Parastoo Qarabaqi, Christopher Murphy, Urbashi Mitra, Gaurav S. Sukhatme, Milica Stojanovic, Hanumant Singh and Franz Hover. "Underwater Data Collection Using Robotic Sensor Networks". In IEEE Journal on Selected Areas in Communications, 30(5):899-911, Jun 2012.
6. P. E. Hagen; (http://ieeexplore.ieee.org/search/searchresult.jsp?newsearch=true) N. Storkersen; (http://ieeexplore.ieee.org/search/searchresult.jsp?newsearch=true) K. Vestgard; (http://ieeexplore.ieee.org/search/searchresult.jsp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) P. Kartvedt (http://ieeexplore.ieee.org/search/searchresult.jsp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) Oceans 2003. Celebrating the Past ... Teaming Toward the Future (IEEE Cat. No.03CH37492) (http://ieeexplore.ieee.org/xpl/mostRecentIssue.jsp?punumber=9015) Year: 2003, Volume: 2
7. Sensor-Driven Online Coverage Planning for Autonomous Underwater Vehicles (http://ieeexplore.ieee.org/document/6304931/) Liam Paull; (http://ieeexplore.ieee.org/search/searchresult.jsp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) Sajad Saeedi; (http://ieeexplore.ieee.org/search/searchresult.jsp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) Mae Seto; (http://ieeexplore.ieee.org/search/searchresult.jsp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) Howard Li (http://ieeexplore.ieee.org/search/searchresult.jsp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) IEEE/ASME Transactions on Mechatronics (http://ieeexplore.ieee.org/xpl/RecentIssue.jsp?punumber=3516) Year: 2013, Volume: 18, Issue: 6 (http://ieeexplore.ieee.org/xpl/tocresult.jsp?isnumber=6681918)
8. Autonomous underwater vehicles for scientific and naval operations Annual Reviews in Control, Volume 30, Issue 2, 2006
9. C. Goudey, T. Consi, J. Manley, M. Graham, B. Donovan, and L Kiley, ―A Robotic Boat for Autonomous Fish Tracking,‖ Marine Technology Society Journal Vol. 32 No. 1, Spring 1998.
10. Caccia M., Bono R., Bruzzone Ga., Bruzzone Gi., Spirandelli E., Veruggio G., Stortini A.M., Capodaglio G.: "Sampling sea surfaces with SESAMO", Robotics and Automation Magazine, vol. 12, no. 3, pp.95-105, 2005
11. J. E. Manley, ―Development of the autonomous surface craft ACES,‖ in IEEE Oceans, 1997.
12. T. Vaneck, C. Rodriguez-Ortiz, M. Schmidt, and J. Manley, ―Automated bathymetry using an autonomous surface craft,‖ Navigation: Journal of the Institute of Navigation, vol. 43, no. 4, 1996.
13. J. E. Manley, A. Marsh, W. Cornforth, and Wiseman, ―Evolution of the autonomous surface craft autocat,‖ in IEEE Oceans, 2000.

14. P. Newman, ―MOOS — a mission oriented operating suite,‖ Department of Ocean Engineering, Massachusetts Institute of Technology, Tech. Rep.,2002.
15. L. L. Whitcomb, D. R. Yoerger, and H. Singh, ―Combined Doppler/LBL based navigation of underwater vehicles,‖ in Proc. Int. Symp. on Unmanned Untethered Submersible Technology, 1999.
16. J. Vaganay, J. Leonard, J. Curcio, and S. Willcox, ―AOFNC – experimental validation of the moving long base line navigation concept,‖ in AUV 2004, June 2004.
17. Data collection, storage, and retrieval with an underwater sensor network, (http://dl.acm.org/citation.cfm?id=1098936) Iuliu Vasilescu, Keith Kotay, Daniela Rus, Matthew Dunbabin, Peter Corke Publication date 2005/11/2
18. M Dunbabin, A Grinham, J Udy, An autonomous surface vehicle for water quality monitoring, Australasian Conference on Robotics and Automation (ACRA), 2-4
19. Seaglider: a long-range autonomous underwater vehicle for oceanographic research (http://ieeexplore.ieee.org/document/972073/)
C. C. Eriksen; (http://ieeexplore.ieee.org/search/searchresult.jsp?newsearch=true) T. J. Osse; (http://ieeexplore.ieee.org/search/searchresult.jsp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) R. D. Light; (http://ieeexplore.ieee.org/search/searchresult.jsp?newsearch=true) T. Wen; (http://ieeexplore.ieee.org/search/searchresult.jsp?searchWithin=%22Authors%22:.QT.T.%20Wen.QT.&newsearch=true) T. W. Lehman; (http://ieeexplore.ieee.org/search/searchresult.jsp?newsearch=true) P. L. Sabin; (http://ieeexplore.ieee.org/search/searchresult.jsp?newsearch=true) J. W. Ballard; (http://ieeexplore.ieee.org/search/searchresult.jsp?newsearch=true) A.M. Chiodi (http://ieeexplore.ieee.org/search/searchresult.jsp?newsearch=true) IEEE Journal of Oceanic Engineering (http://ieeexplore.ieee.org/xpl/RecentIssue.jsp?punumber=48) Year: 2001, Volume: 26
20. Elgar Desa, R. Madhan and P. Maurya, Potential of autonomous underwater vehicles as new generation ocean data platforms, Current Science Vol. 90, No. 9 (10 May 2006), pp. 1202-1209
21. C Spampinato, YH Chen-Burger, G Nadarajan, RB Fisher, Detecting, Tracking and Counting Fish in Low Quality Unconstrained Underwater Videos., VISAPP (2) 2008, 514-519
M Dunbabin, L Marques, Robots for environmental monitoring: Significant advancements and applications, IEEE Robotics & Automation Magazine 19 (1), 24-39

Acknowledgements

### We would like to acknowledge the guidance given to us by faculty

and staff of our department. Most importantly, we thank our guide Prof.

### Ankit Khivasara and Prof. Avinash Prabhudesai for undertaking our responsibility and continuously monitoring our work, avoiding obstacles and providing feedback at all stages much like our Autonomous Water Rover itself. It would not have been possible without their ideologies for us to win

3 National Level competitions with this project.

### We are also grateful to Dr. Shubha Pandit (Principal, K.J.Somaiya

College of Engineering) and Dr. Ameya Naik (Head of Department,

### Electronics and Telecommunication Branch) for their continuous encouragement during our project journey. Special thanks to the senior members at Team KJSCE Robocon, for their continuous tech support. We are thankful to our colleagues for providing a competitive atmosphere for us

to bloom.

Last, but not the least, we wish to thank our parents and the tiffins.

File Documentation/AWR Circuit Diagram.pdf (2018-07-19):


Scanned by CamScanner

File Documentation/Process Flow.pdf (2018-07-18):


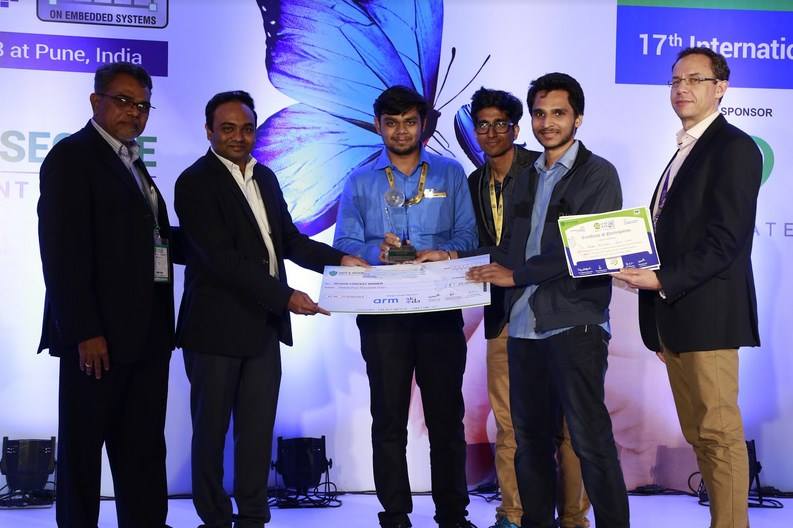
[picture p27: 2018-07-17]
Project Images/Project Competitions/design contest.jpg

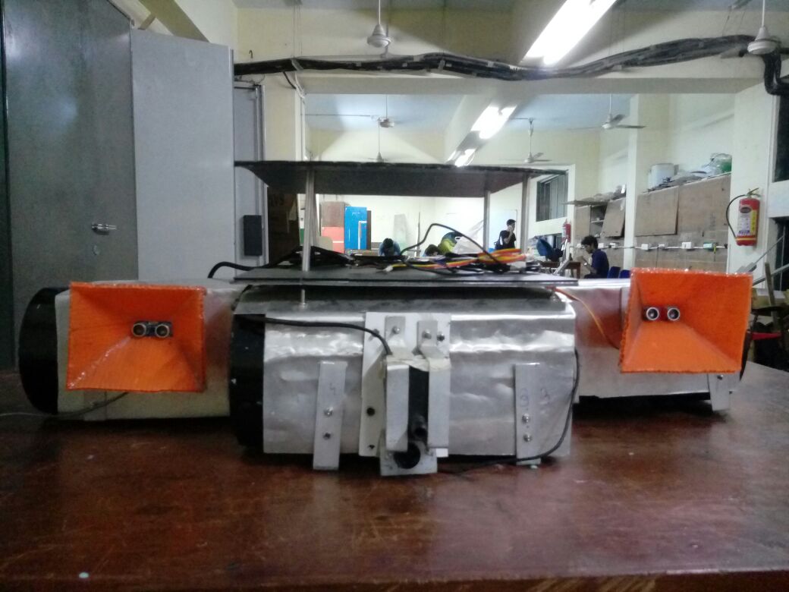
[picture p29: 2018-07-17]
Project Images/Autonomous Water Rover Photos/Front View.jpg

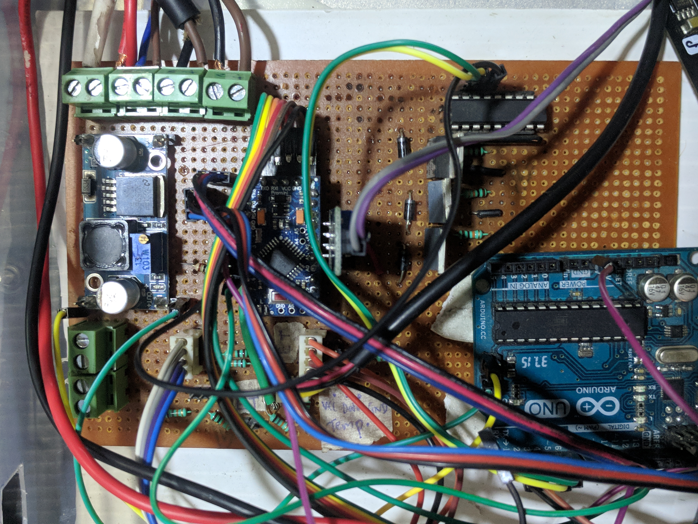
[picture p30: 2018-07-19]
Documentation/Circuit Image.jpg

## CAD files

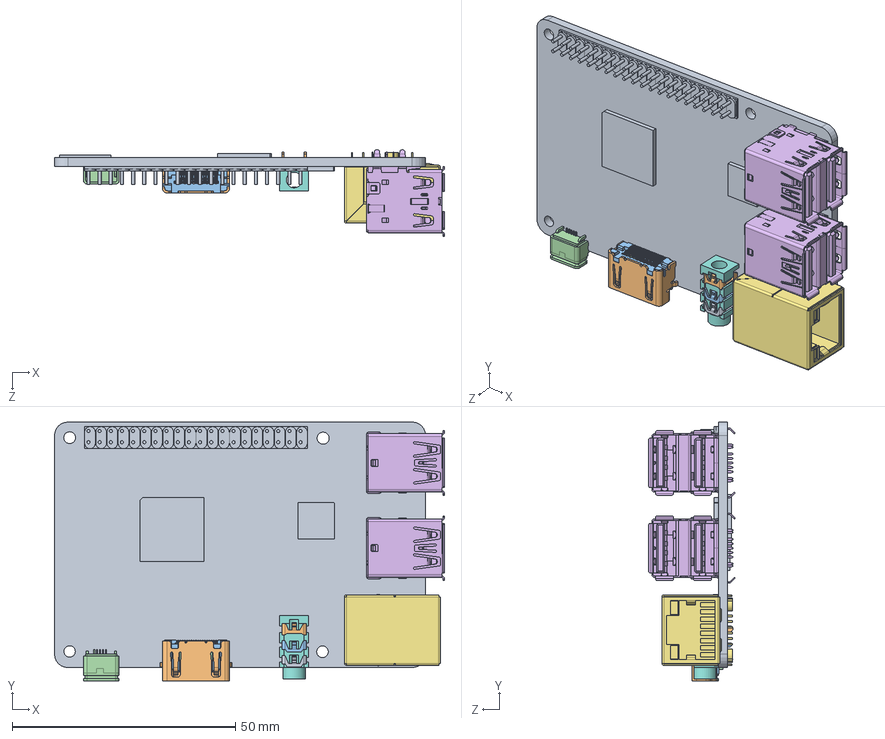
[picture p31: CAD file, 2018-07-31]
Solidworks Design Files/raspberry_carte.SLDASM
87.4 x 58.0 x 19.4 mm
carte_mere
HDMI_socket_cover
HDMI_socket_inside
HDMI_socket_large_pin x 10
HDMI_socket_small_pin x 9
usb3x2 x 2
RJ45_10P_TJ3009
PCB_Stereo_Jack_(body)
PCB_Stereo_Jack_(GND_contact)
PCB_Stereo_Jack_(channel_contact_2)
PCB_Stereo_Jack_(channel_contact_1)
USB

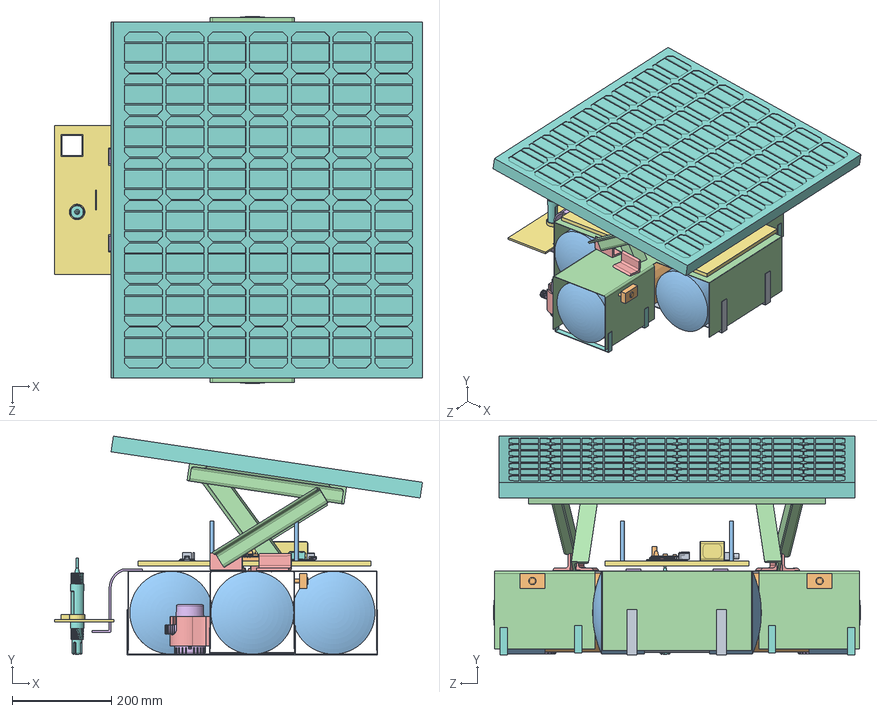
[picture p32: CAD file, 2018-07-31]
Solidworks Design Files/exhibit.SLDASM
741.7 x 441.0 x 740.0 mm
raft_front x 2
raft_middle
pipe cap x 6
top
pump housing_1 x 2
B-700021 x 2
Turnigy_5000mAh_4S__nano_tech_Lipo_Battery
Sonde PH
Interface PH
dc motor driver shield
carte_mere
HDMI_socket_cover
HDMI_socket_inside
HDMI_socket_large_pin x 10
HDMI_socket_small_pin x 9
usb3x2 x 2
RJ45_10P_TJ3009
PCB_Stereo_Jack_(body)
PCB_Stereo_Jack_(GND_contact)
PCB_Stereo_Jack_(channel_contact_2)
PCB_Stereo_Jack_(channel_contact_1)
USB
layer
bottom support x 4
bottom support centre x 2
ultrasound+mounting o x 2
v_spacer x 4
solar panel 670x630
panel L mounting x 4
slide guide x 2
sensor mount
panel new

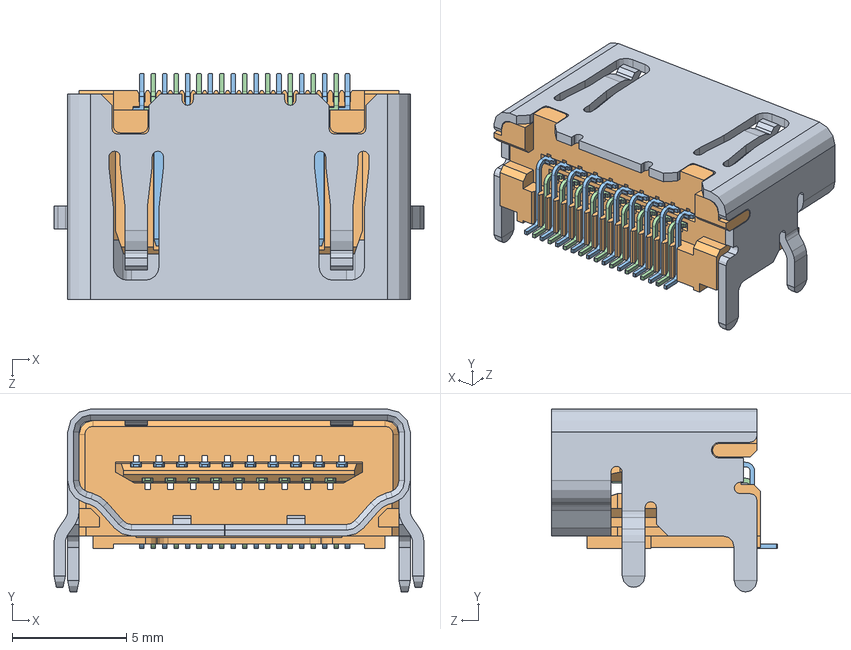
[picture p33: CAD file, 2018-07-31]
Solidworks Design Files/HDMI_socket.SLDASM
16.2 x 8.00 x 9.90 mm
HDMI_socket_cover
HDMI_socket_inside
HDMI_socket_large_pin x 10
HDMI_socket_small_pin x 9

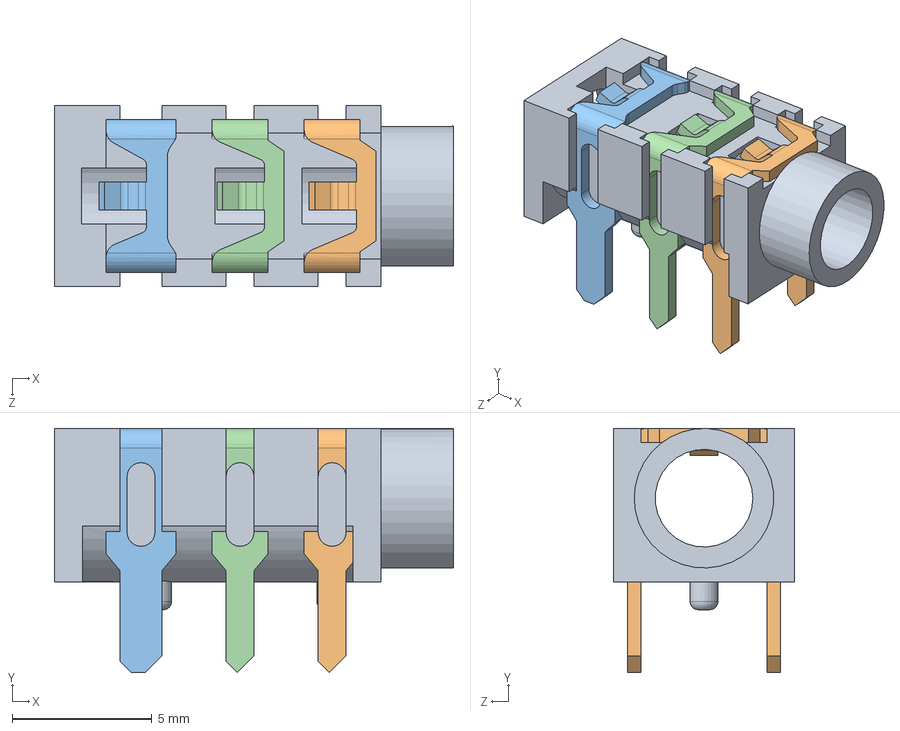
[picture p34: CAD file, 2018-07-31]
Solidworks Design Files/PCB_Stereo_Jack_(assembly).SLDASM
14.3 x 8.75 x 6.50 mm
PCB_Stereo_Jack_(body)
PCB_Stereo_Jack_(GND_contact)
PCB_Stereo_Jack_(channel_contact_2)
PCB_Stereo_Jack_(channel_contact_1)

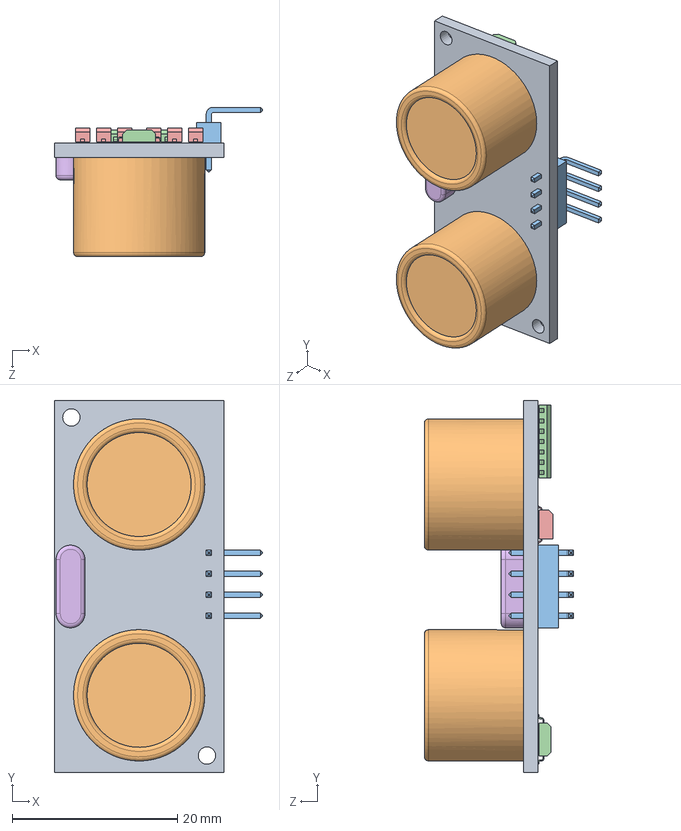
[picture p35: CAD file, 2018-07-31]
Solidworks Design Files/HC-SR04 Ping Sensor.SLDASM
25.2 x 45.0 x 18.1 mm
PCB
Transducer x 2
3 Pin Header 90 Degree
14 Pin SMT x 3
Cap1 SMT x 6
HC-SR04 Crystal.SLDASM

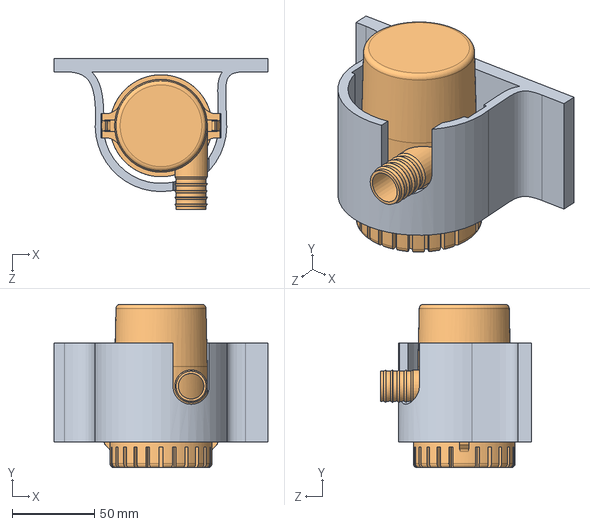
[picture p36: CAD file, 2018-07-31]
Solidworks Design Files/Assem4.SLDASM
130.0 x 99.3 x 91.6 mm
pump housing_1
B-700021

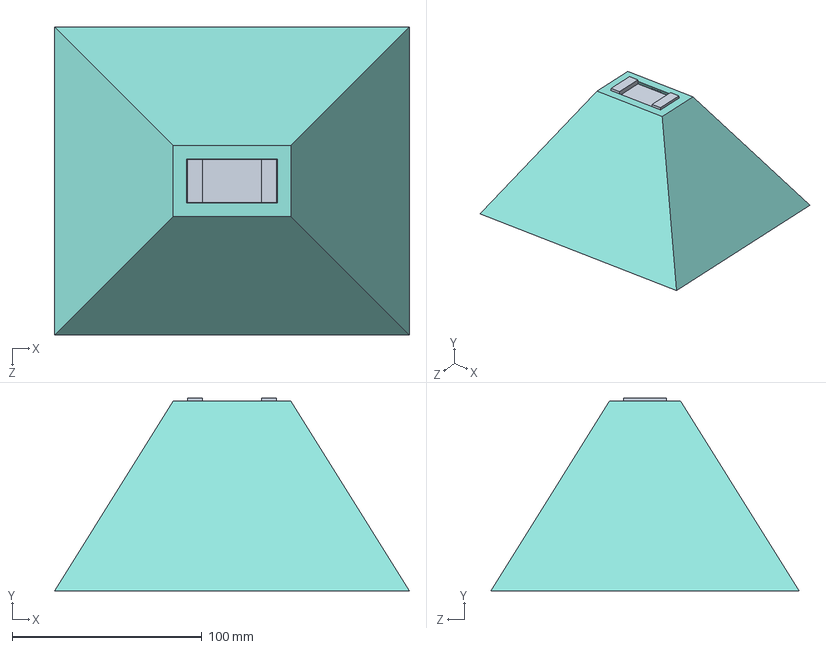
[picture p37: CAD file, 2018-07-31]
Solidworks Design Files/ultrasound_assm.SLDASM
187.0 x 101.6 x 162.5 mm
ultrasound_backmounting
PCB
Transducer x 2
3 Pin Header 90 Degree
14 Pin SMT x 3
Cap1 SMT x 6
HC-SR04 Crystal.SLDASM
horn_angenna

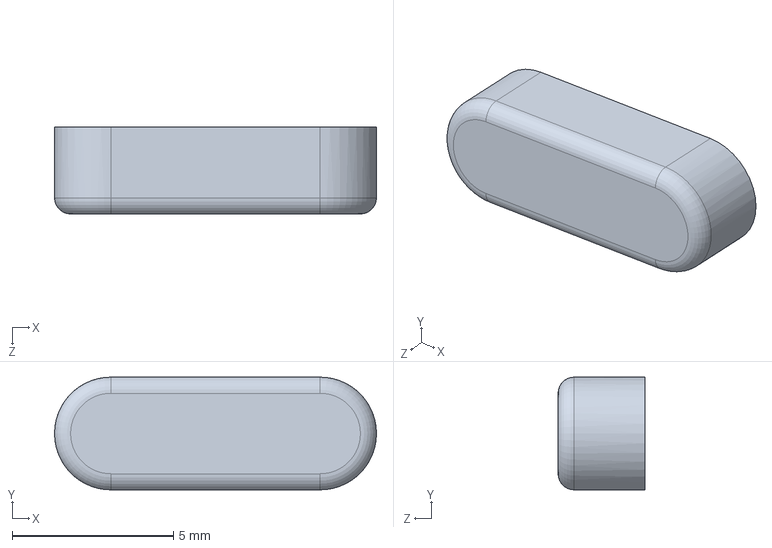
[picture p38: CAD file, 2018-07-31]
Solidworks Design Files/HC-SR04 Crystal.SLDASM.SLDPRT
10.0 x 3.50 x 2.70 mm

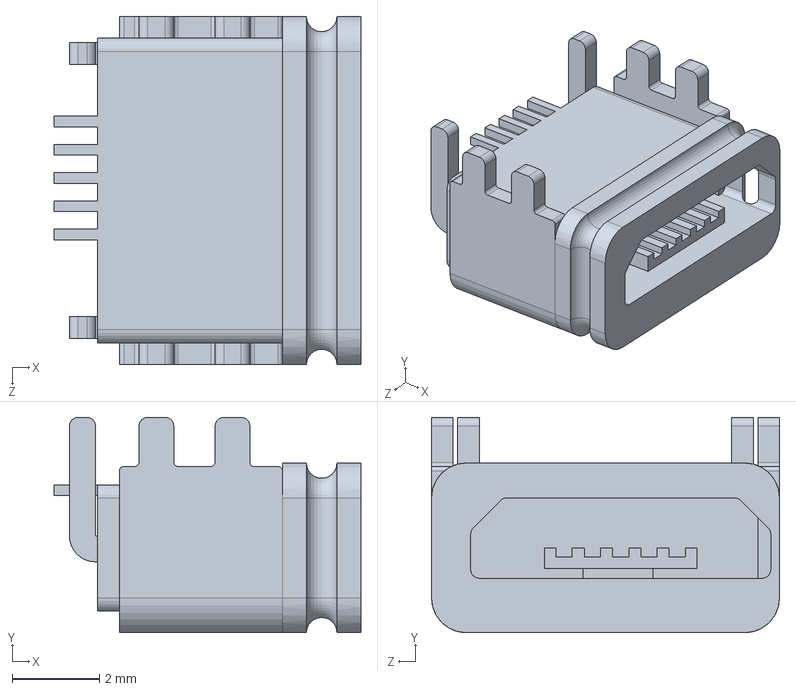
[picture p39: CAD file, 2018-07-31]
Solidworks Design Files/USB.sldprt
7.05 x 4.95 x 8.00 mm

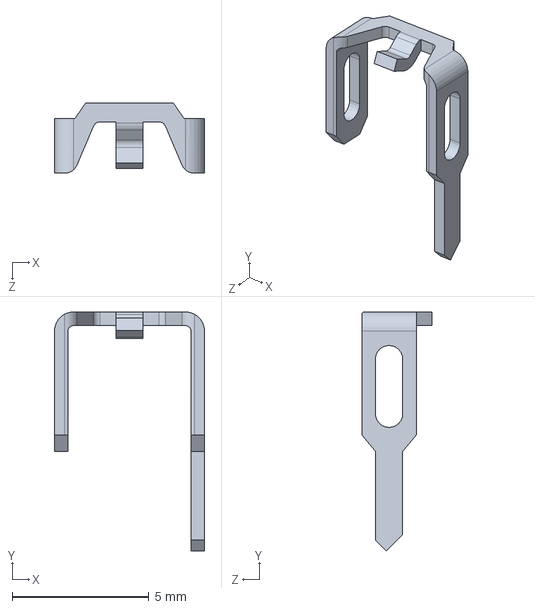
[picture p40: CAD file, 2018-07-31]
Solidworks Design Files/PCB_Stereo_Jack_(channel_contact_1).SLDPRT
5.50 x 8.75 x 2.58 mm

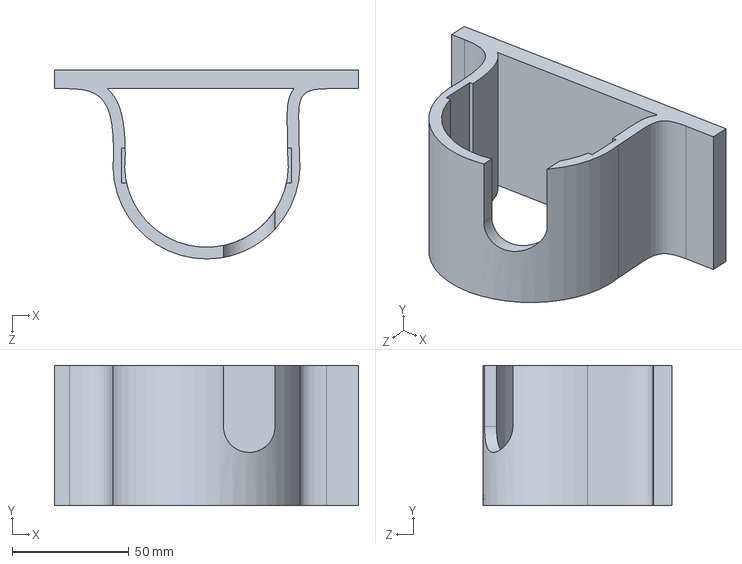
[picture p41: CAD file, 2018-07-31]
Solidworks Design Files/pump housing_1.SLDPRT
130.0 x 60.0 x 80.8 mm

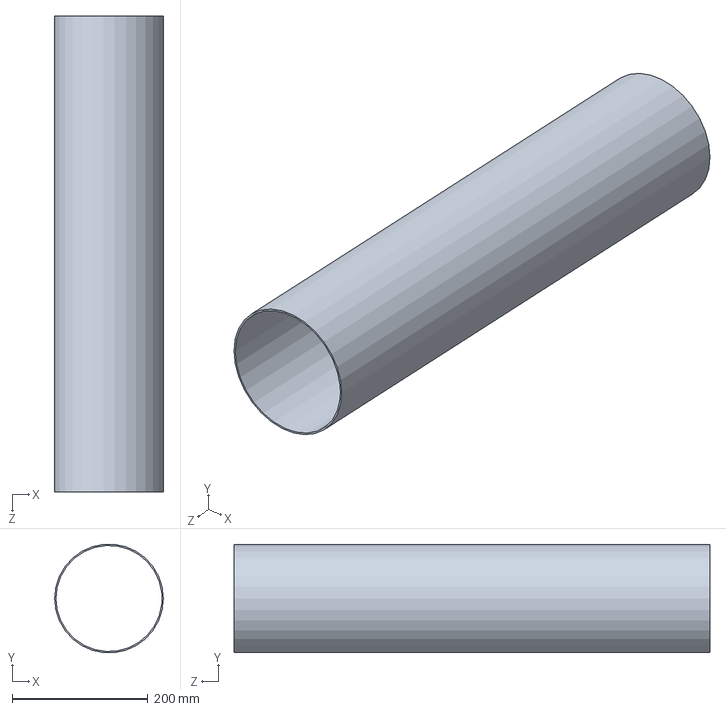
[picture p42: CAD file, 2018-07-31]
Solidworks Design Files/raft_middle.SLDPRT
160.0 x 159.1 x 700.0 mm

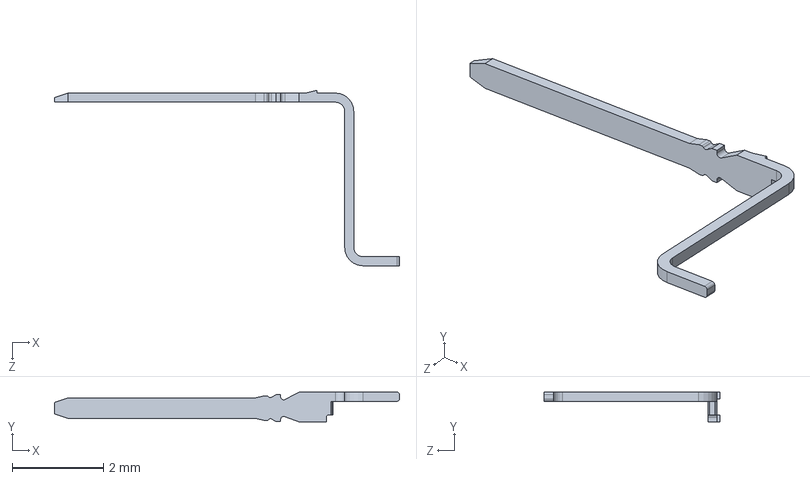
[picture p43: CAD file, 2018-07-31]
Solidworks Design Files/HDMI_socket_large_pin.SLDPRT
7.55 x 0.65 x 3.84 mm

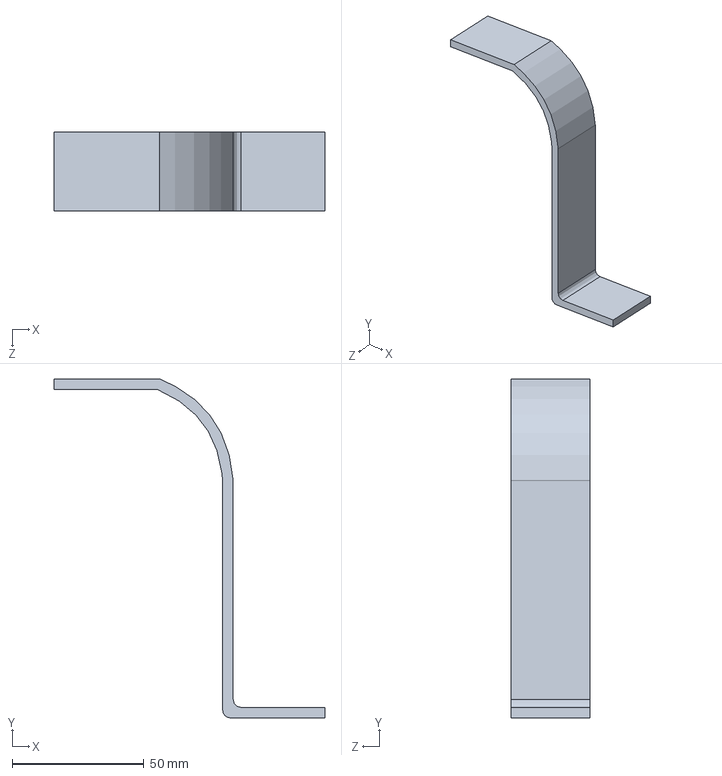
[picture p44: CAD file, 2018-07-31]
Solidworks Design Files/slide guide.SLDPRT
102.5 x 128.4 x 30.0 mm

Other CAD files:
Solidworks Design Files/bottom support centre.SLDPRT
Solidworks Design Files/sensor mount.SLDPRT
Solidworks Design Files/carte_mere.SLDPRT
Solidworks Design Files/ultrasound+mounting o.SLDPRT
Solidworks Design Files/14 Pin SMT.SLDPRT
Solidworks Design Files/3 Pin Header 90 Degree.SLDPRT
Solidworks Design Files/B-700021.SLDPRT
Solidworks Design Files/Cap1 SMT.SLDPRT
Solidworks Design Files/HDMI_socket_cover.SLDPRT
Solidworks Design Files/HDMI_socket_inside.SLDPRT
Solidworks Design Files/HDMI_socket_small_pin.SLDPRT
Solidworks Design Files/Interface PH.SLDPRT
Solidworks Design Files/PCB.SLDPRT
Solidworks Design Files/PCB_Stereo_Jack_(GND_contact).SLDPRT
Solidworks Design Files/PCB_Stereo_Jack_(body).SLDPRT
Solidworks Design Files/PCB_Stereo_Jack_(channel_contact_2).SLDPRT
Solidworks Design Files/RJ45_10P_TJ3009.SLDPRT
Solidworks Design Files/Sonde PH.SLDPRT
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

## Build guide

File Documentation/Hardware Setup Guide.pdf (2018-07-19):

Hardware Setup Information

The system diagram of the Autonomous Water Rover is as follows :

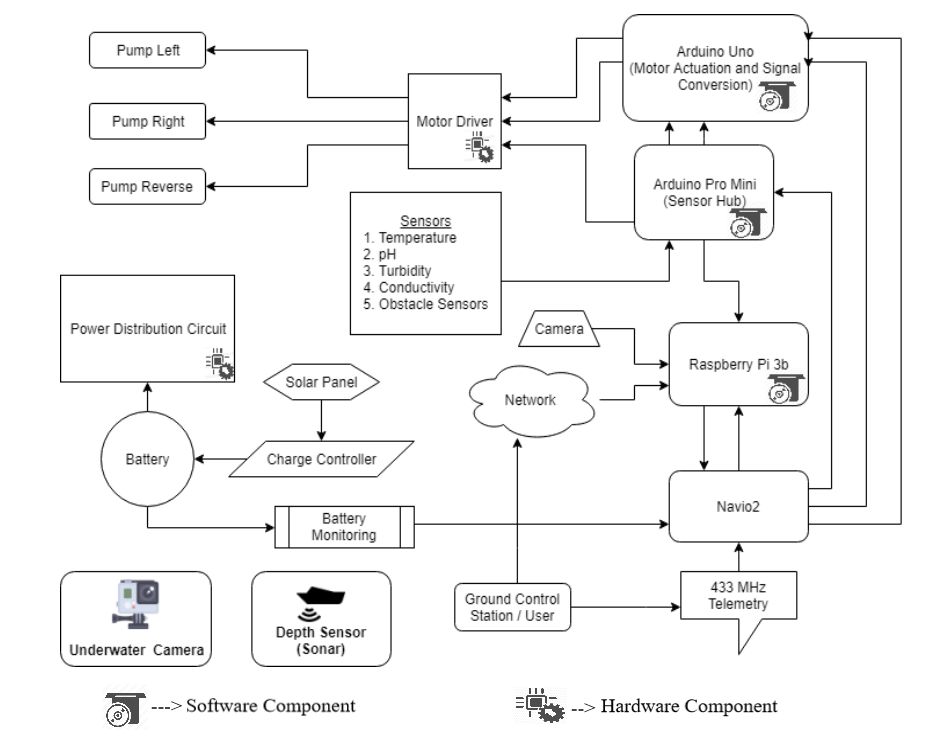
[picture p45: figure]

Figure 1 System Diagram

The various components in the above figure are as follows :-
- Power System: The power generation, storage and distribution includes the following main components :
- Battery : LiPo will be used to ensure operation of rover for over an hour on one charging
- Solar Panel : A 50W Solar Panel is used to charge the 12 volt battery and also increase the operation period

- Charge Controller : A 20A 12V waterproof solar panel charge controller will be used
- Voltage regulation : Voltage regulators will be used to always keep the supply voltage for the pumps constant i.e. 12V to obtain similar performance even at different battery levels. Also 5V and 3.3V voltage regulators will be used for obtaining required supply voltage for the Rpi controller board, Navio2, telemetry and all installed sensors on the rover
- Raspberry Pi 3b : It is a single board computer which will be used for complex path planning through ardupilot, hosting the web interface, providing live video streaming and communicating with sensor nodes
- Navio2 : It is an autopilot Hat for Raspberry Pi 3b which simplifies autonomous navigation by bringing multiple sensors on a single board and by seamless integration with Raspberry Pi. It also has analog to digital converters along with pulse generators to produce pulses which can control servo motors. The following sensors will be used by the Autonomous Water Surveillance Rover :
- GNSS Receiver : Tracks GPS, GLONASS, Beidou, Galileo and SBAS satellites for accurate positioning
- Dual IMU : Accelerometers, gyroscope and magnetometer readings will be used for orientation and motion sensing
- High resolution barometer : Senses altitude with 10 cm resolution and can be used to relay accurate location information along with GPS
- Communication Ports : UART interface will be used to relay information through telemetry radio
- Ground Control Station : It could be any windows based personal computer having Mission Planner installed
- Local Area Network : A LAN is created to access the website hosted on the raspberry pi. It is not needed for operation in autonomous mode

- Telemetry Radio : The mRo SiK Telemetry Radio V2 operates at 433Mhz and provides 300m range by default. This radio will be the link to relay localization details and program missions for the rover remotely
- Underwater Camera : A GoPro hero is used to gather images of the underwater bed upto three meters. As penetration of light at this depth is sufficient, an illuminating light source will not be necessary. The light source can be fitted to the base of the rover for illumination if surveillance is to be done in the absence of sunlight
- Camera : A raspberry pi camera version 2 is used to provide live first person view of the rover to operator
- Sensor Node : Data acquisition from the environment will carried out and the information will be relayed to the Rpi. An arduino pro mini is used because of its small form factor for interfacing the sensors and communicating with raspberry pi
- Distance Sensors : Two waterproof ultrasound (40 KHz) distance sensors i.e. JSN-SR04T are used to detect obstacles on the surface of the water and in the forward path of the rover
- Water Quality Monitoring Sensors : To measure the quality of water following parameters are being measured :-
- pH : DFRobot Gravity : analog pH sensor is being used to measure the pH of water. The pH measurements have a resolution of ± 0.1pH at 25 ℃
- Temperature : DS18B20 waterproof temperature sensor probe is used to get ±0.5°C accuracy in the range -10°C to +85°C. It uses 1-Wire interface i.e. requires only one digital pin for communication
- Conductivity : A generic rain sensitive sensor module is used in analog mode to get the conductivity readings. The accuracy of this module for measuring isn’t high but can be used for thresholding purposes
- Turbidity : DFRobot Gravity : analog turbidity sensor is used to obtain the turbidity readings which is later converted to NTU units.

- Fish Finder : ZEEPIN Fish Finder is a wireless & rechargeable sonar sensor along with a smart portable LCD display which is used to get depth data, temperature data along with the add on of identifying fishing areas
- Signal Converter : The output signal from the Navio 2 is in the form of RC pulses of the duration 1ms to 2ms. The external interrupt pins of an arduino uno is used to measure the pulse widths of these pulses and accordingly generate a PWM signal which drives the motor driver circuit
- Motor Driver Circuit : The arduino uno will send control signals to the motor driver which in turn will control the actuator i.e. pumps. The pumps will be operated at variable speed according to navigation control using PWM to allow more precise control over the rover

Hardware Design

Hardware design has three main components. They involve the power distribution circuit, the motor driver circuit and other peripheral device connections. A circuit as shown below was designed to reduce wire connections and also to simplify sensor interfacing. It includes the power distribution system, the motor driver circuits and sensor input slots for the Arduino Pro Mini.

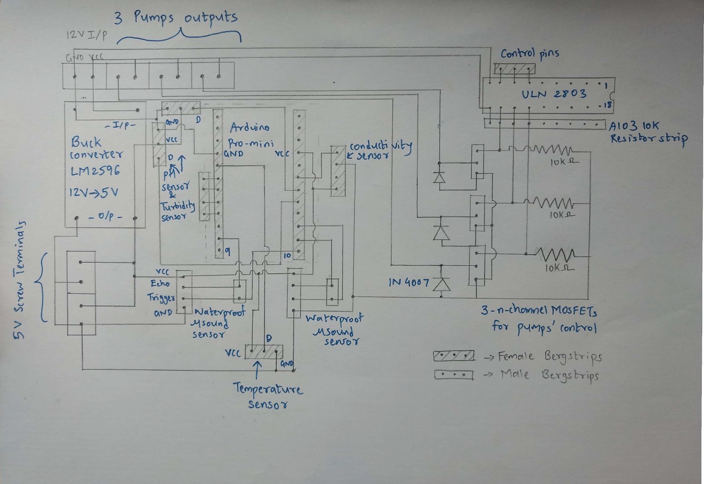
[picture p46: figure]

Figure 2 Circuit Diagram

Step 1
- The foremost thing to figure out is the motor control on the right hand side of the diagram. Since we are using bilge pumps, only unidirectional control is required eliminating the need for a H-bridge configuration.

- The ULN 2803 has Darlington pair transistors which are being used to provide the Gate of the n-channel Mosfets with the corresponding voltages. A point to remember is that the ULN 2803 will complement the output, thus a 0v i/p is to be given for a high output and vice versa.
- The Gate terminal is to be grounded with a high value resistor (10k ohms) since the Mosfet is a voltage controlled device.
- The Resistor strip A103 helps to keep the output of the ULN 2803 at a stable output. Thus, by giving complementary i/ps to the ULN 2803, we can control the pump motors.

Motor Driver Circuit

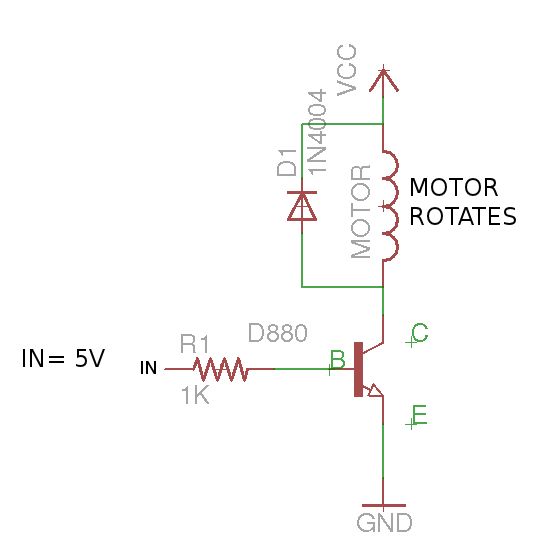
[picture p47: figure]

Fig 3 MOSFET schematic
Fig 3 shows the basic controlling of a motor using a MOSFET.

The total cost for the board is Rs. 561/8.25$

Step 2
Power Distribution Circuit
The 12V Lipo battery is connected to a General Purpose Board on which different circuits of the system are soldered. The voltage is stepped down for powering the sensors and the microcontroller board, using a LM2596 buck converter which step downs the voltage from 12V to 5V. The circuit is soldered on a General Purpose Board as shown in figure 2
Step 3
- The peripheral devices include the RPI 3b, Navio 2, Arduino Pro Mini, Arduino Uno and sensors. After Navio2 is mounted on RPI we have to proceed and attach other peripherals and wires for communication and sensors. The connection diagram is as follows :-

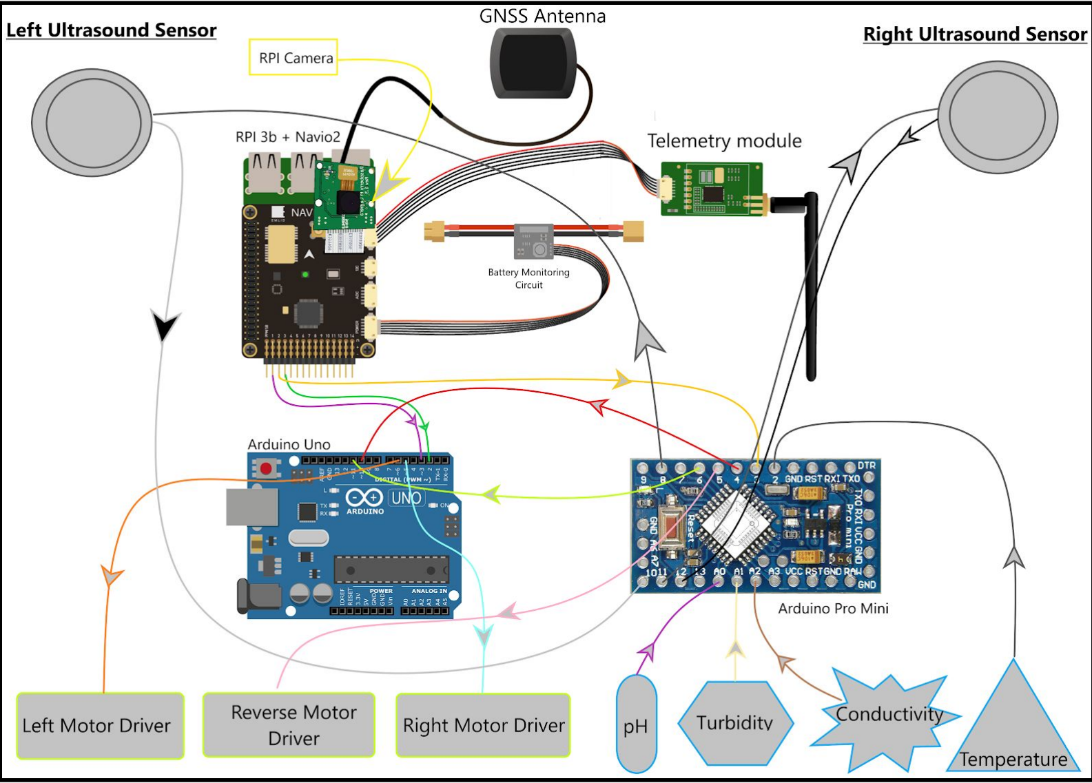
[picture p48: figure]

- Arduino Pro-mini shield in figure 2 is made using female bergstrips and the data pins of all the 4 sensors are connected to the corresponding pins as shown in above figure.
- The ultrasound sensors are also connected with their echo and trigger pins. All the sensors and the Pro-mini are powered by the LM 2596 buck converter which gives a 3A/5V output.

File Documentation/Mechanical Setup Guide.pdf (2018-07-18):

Mechanical Setup

Highlights:

- Low-cost
- Easy to make
- High payload capacity
- Stable design
Step 1: Calculate total Weight
- Select the equipments and payload to be added on the rover. This decides the total buoyancy required by the rover.
- Once the total weight required is decided, calculate the volume required to be displaced (Archimedes principle).
Buoyant force is given by:

(rho here is density of water)

Note that the total force also includes the weight of the structure (hull) too and not just the payload.

Step 2: Selecting the appropriate propulsion system:
●
- The target waters for the rover are still and weedy waters. Conventional propulsion system has a potential to clog in weeds and needs to be cleared. Instead it was decided to use differential reaction drive for propulsion using two submersible pumps.
- The reaction drive works by having an intake which is located below the hull submerged in water. Water enters the pump through the inlet. The pump is usually centrifugal pump for higher speeds or axial flow type for medium or low speeds. The water pressure in increased inside the pump and is directed outward through a nozzle.

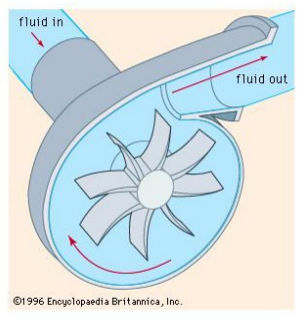
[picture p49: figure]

- The pump selected is Vetus V1000.

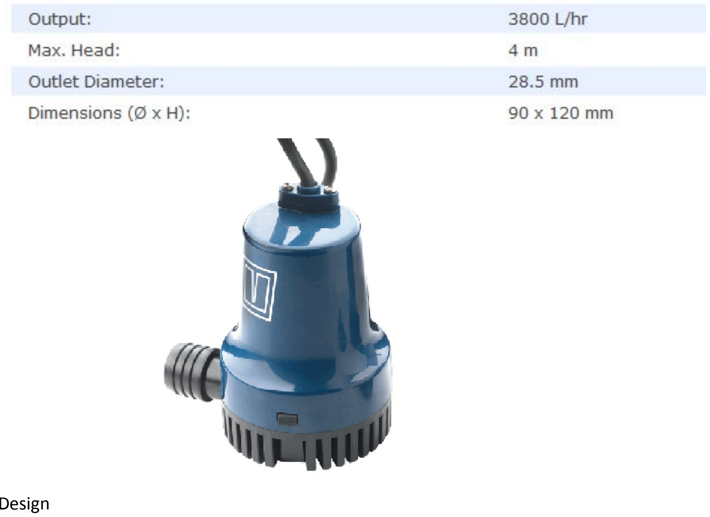
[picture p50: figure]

Step 3: Design
- Select the design of the rover as per the requirement.
- For simple construction and assembly, we have used raft like structure made of PVC pipes.
- We selected PVC pipes of 6” dia (16 cm); took three pipes of length 30 cm, 90 cm and 30 cm each. This gave us the total load capacity of about 30 kg (inclusive of the pipes own weight). Volume of Pipes:
- Model it in CAD:

The relation between center of Buoyancy, center of gravity and the hull shape is very critical for the stability of the rover. CAD provides with the approximate points for their locations.

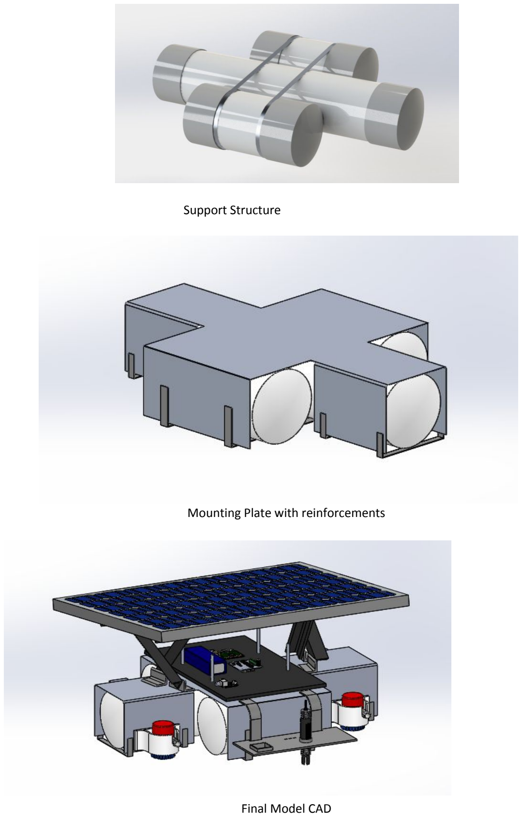
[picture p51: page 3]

Support Structure

Mounting Plate with reinforcements

Final Model CAD

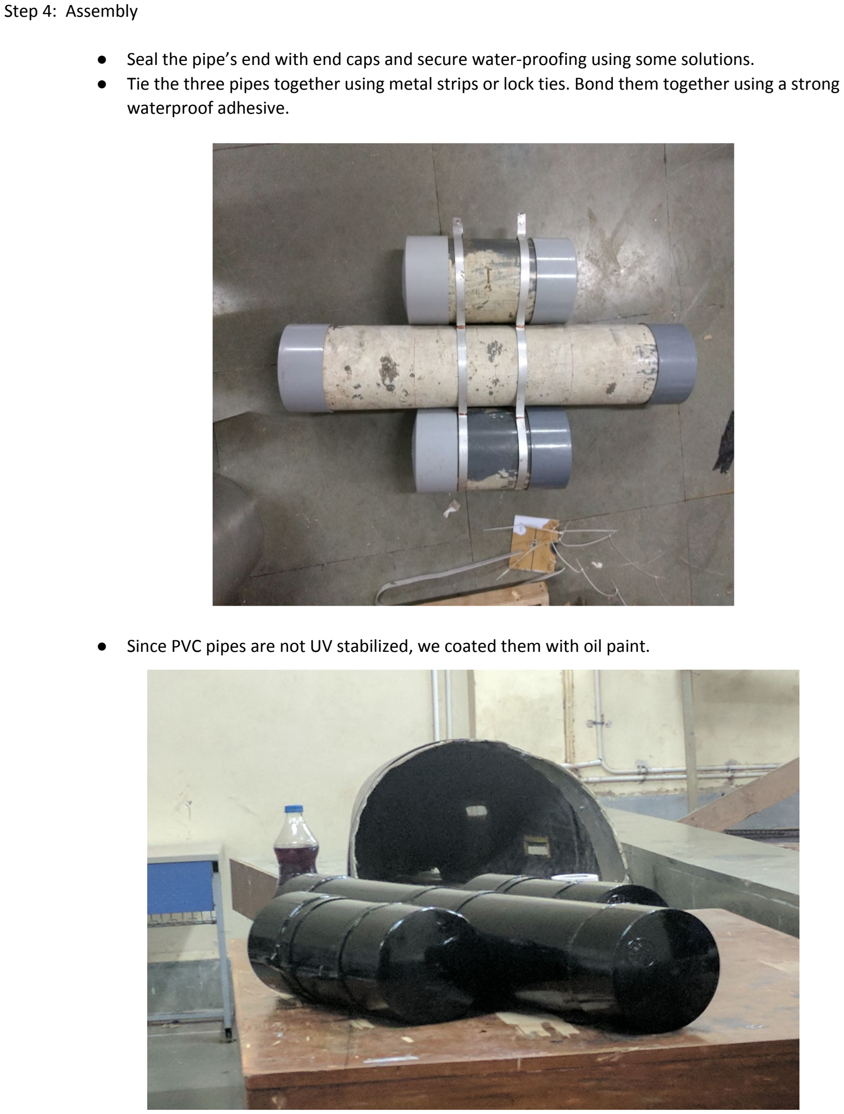
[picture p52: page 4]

Step 4: Assembly
- Seal the pipe’s end with end caps and secure water-proofing using some solutions.
- Tie the three pipes together using metal strips or lock ties. Bond them together using a strong waterproof adhesive.
- Since PVC pipes are not UV stabilized, we coated them with oil paint.

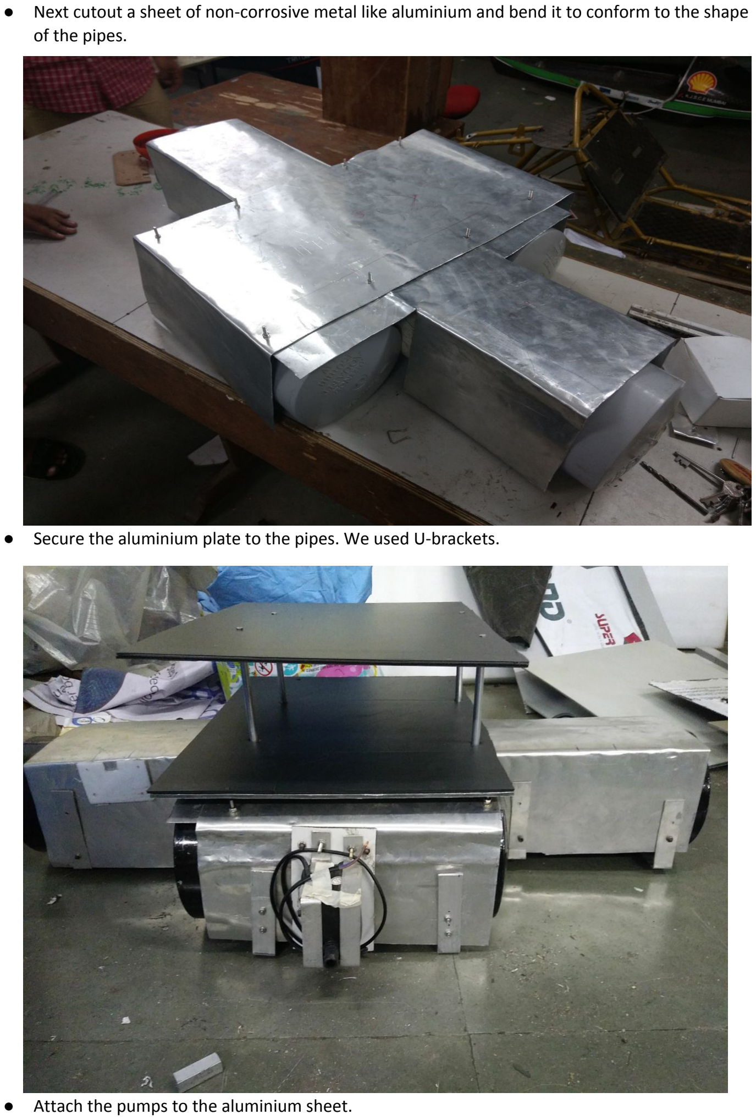
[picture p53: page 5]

- Next cutout a sheet of non-corrosive metal like aluminium and bend it to conform to the shape of the pipes.
- Secure the aluminium plate to the pipes. We used U-brackets.
- Attach the pumps to the aluminium sheet.

●

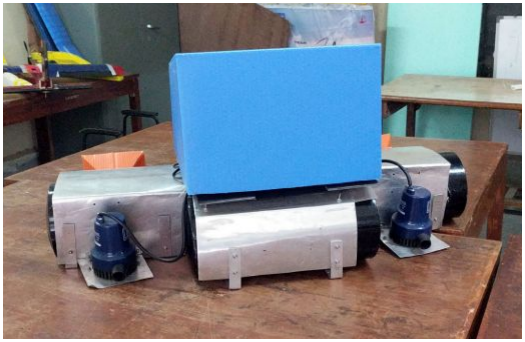
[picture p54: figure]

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
all t

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
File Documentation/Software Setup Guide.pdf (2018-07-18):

Setup the Navio2

- Follow this link to setup the navio2 hardware https://docs.emlid.com/navio2/ardupilot/hardware-setup/

Setting up Raspberry Pi 3b
- Flash memory card with preconfigured image from navio2 website
- Follow the steps from navio 2 website to configure the image for an ardurover https://docs.emlid.com/navio2/common/ardupilot/configuring-raspberry-pi/

Setting up the Ground Control Station
- Mission Planner (only for Windows) http://ardupilot.org/planner/docs/common-install-mission-planner.html

Configuring Autopilot using mission planner
- Follow the link below to setup rover (Skid steering configuration) http://ardupilot.org/rover/index.html

Connecting to RPI using SSH

- Connect phone to same network as raspberry is configured to connect. Use android application “Fing” to find IP address of navio 2, also we can use nmap utility.
- Using windows application “Putty” SSH using the ip obtained in above step.
- Follow navio2 docs to configure the autopilot https://docs.emlid.com/navio2/ardupilot/
- If using configured image network credentials should be
Username : hartznetwork
Password : sunnyday

Setting up Live Video Feed Service

- Setup motion on a web server https://pimylifeup.com/raspberry-pi-webcam-server/
- If unable to access video (gray screen is observed)
Refer the below discussion and try the command “sudo modprobe bcm2835-v4l2” to rectify the situation.
https://raspberrypi.stackexchange.com/questions/60669/unable-to-open-video-device

Setting up Flask Server and IoT platform (Example)

- The below link offers the basic instruction for setting up an ioT platform using Flask http://www.instructables.com/id/From-Data-to-Graph-a-Web-Jorney-With-Flask-and-SQL/ (http://www.instructables.com/id/From-Data-to-Graph-a-Web-Jorney-With-Flask-and-SQL/)
Setting up Remote Page (Example)
- Use below link to control understand controlling rover from web interface https://circuitdigest.com/microcontroller-projects/web-controlled-raspberry-pi-surveilla nce-robot

Understanding tracking on web interface (Example)

- Use below link to get a gist of google maps apis can be used http://www.instructables.com/id/Raspberry-Pi-Location-Tracker/

Understanding programming for web interface (Reference)

- HTML crash course for absolute beginners https://www.youtube.com/watch?v=UB1O30fR-EE
- CSS crash course for absolute beginners https://www.youtube.com/watch?v=yfoY53QXEnI
- Javascript for absolute beginners https://www.youtube.com/watch?v=vEROU2XtPR8&list=PLillGF-RfqbbnEGy3ROiLWk7J MCuSyQtX (https://www.youtube.com/watch?v=vEROU2XtPR8&list=PLillGF-RfqbbnEGy3ROiLWk7JMCuSyQtX)

This Project uses python 2 for its operation kindly ensure you install dependencies for python 2 only.

Note :
- Tunneling local server to the internet can be done to remove restriction of LAN
- Can be done using Pagekite or Ngrok

Reference Links used to add various features on the web interface

- UI Tab feature
https://codepen.io/samarkandiy/pen/AiGjs

- Flask Buttons
http://www.instructables.com/id/Python-WebServer-With-Flask-and-Raspberry-Pi/
- Flask Database
http://www.instructables.com/id/From-Data-to-Graph-a-Web-Jorney-With-Flask-and-SQL/ (http://www.instructables.com/id/From-Data-to-Graph-a-Web-Jorney-With-Flask-and-SQL/)
- Graphs using Python and sqlite https://www.fontenay-ronan.fr/dynamic-charts-with-highcharts-sqlite-and-python/
- Multiple Tabs
https://codepen.io/samarkandiy/pen/AiGjs
- Side by Side divisions
https://jsfiddle.net/c6242/1/
- Data display
http://www.instructables.com/id/From-Data-to-Graph-a-Web-Jorney-With-Flask-and-SQ/
- Image Gallery
https://www.w3schools.com/css/tryit.asp?filename=trycss_image_gallery
- Button
https://www.w3schools.com/css/css3_buttons.asp
- Flask error
https://stackoverflow.com/questions/31252791/flask-importerror-no-module-named-fl ask (https://stackoverflow.com/questions/31252791/flask-importerror-no-module-named-flask)
- Maps
https://developers.google.com/maps/documentation/javascript/adding-a-google-map
- Asynchronous update location https://www.shanelynn.ie/asynchronous-updates-to-a-webpage-with-flask-and-socket-io/ (https://www.shanelynn.ie/asynchronous-updates-to-a-webpage-with-flask-and-socket-io/)
https://blog.miguelgrinberg.com/post/easy-websockets-with-flask-and-gevent
- Installing socket libraries for python

Pip install flask-socketio
pip uninstall python-socketio pip install python-socketio
Pip install eventlet
- If conflict arises between sqlite and socket go to below link https://stackoverflow.com/questions/393554/python-sqlite3-and-concurrency

### Navio 2 Reference Links

Emlid Documentation

- Flashing card and network configuration https://docs.emlid.com/navio2/common/ardupilot/configuring-raspberry-pi/

Autopilot tutorial

- https://docs.emlid.com/navio2/common/ardupilot/installation-and-running/

Github examples

- https://github.com/emlid/Navio2

ROS

- http://wiki.ros.org/Robots/Navio2

Tutorials for navio2 other than Emlid docs

Trello
https://trello.com/c/reCjd6Ls/90-mavros-navio2-tutorial

Instructable
http://www.instructables.com/id/Getting-Started-With-NavioNavio2/

Hackaday
https://hackaday.io/project/16352/instructions

DC motor control
https://community.emlid.com/t/how-to-control-a-dc-motor/353/4

Mavlink bridge
http://ardupilot.org/dev/docs/making-a-mavlink-wifi-bridge-using-the-raspberry-pi.html

ROS & Gazebo
http://gazebosim.org/tutorials?tut=ros_gzplugins#DifferentialDrive

ADC
https://community.emlid.com/t/read-adc-and-gpio17-18-into-python-script-while-apm-running/63 41 (https://community.emlid.com/t/read-adc-and-gpio17-18-into-python-script-while-apm-running/6341)

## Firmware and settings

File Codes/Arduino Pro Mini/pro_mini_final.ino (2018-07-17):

# /*
#   *
#   * Project Name:     Autonomous Water Rover
#   * Author List:      Chirag Shah
#   * Filename:        dataAquisition.ino
#   * Functions:        averagearray(), phRead(),rainRead(),turbRead(),tempRead()
#   * Global Variables: pH,turb,rain,Offset, samplingInterval, printInterval, ArrayLenth,
                        LED ,trigPin1,echoPin1,trigPin2,echoPin2 ,duration,distance,duration2,distance2;
                        pHArray[ArrayLenth],pHArrayIndex=0,turbArray[ArrayLenth],turbArrayIndex=0,tempArray[ArrayLenth],tempArrayIndex,
                        rainArray[ArrayLenth],rainArrayIndex, rainVoltage,pHValue,turbVoltage,temp, ONE_WIRE_BUS 2
#   * Description: This file is used to read sensor data from the sensors and apply an averaging filter to them
# */
#include <OneWire.h> 
#include <DallasTemperature.h>

#define ONE_WIRE_BUS 2 //Data of temp sensor at pin2

OneWire oneWire(ONE_WIRE_BUS); 
DallasTemperature sensors(&oneWire);

#define pH A0            //pH meter Analog output to Arduino Analog Input 0
#define turb A1   //turbidity meter Analog output to Arduino Analog Input 1
#define rain A2  //conductivity meter Analog output to Arduino Analog Input 2
#define Offset 0.13            //deviation compensate for pH
#define samplingInterval 20 //Time after which reading is noted
#define printInterval 8000 //Time after which data is sent to pi
#define ArrayLenth  40    //times of collection
#define LED 13
#define MinPulseLength 1100  // these are RC output obtained fromm Navio2
#define MaxPulseLength 1900

int RCinputPinRev = 3;//physical pin mapping on uno
int pin3interruptRev = 1; //ext interrupt 1
int PWM_PinRev = 5; // PWM output pins
unsigned long volatile RCpulseLastChangeTime = 0; //Timeout constant
int pulseLengthRev=0;

const int trigPin1 = 8;//m1/Left side 
const int echoPin1 = 10;
const int trigPin2 = 11;//m2/Right side
const int echoPin2 = 12;
long duration; //Left distance sensor pulse duration
int distance; //Left distance sensor reading in cm after computation
long duration2; //Right distance sensor pulse duration
int distance2; ////Right distance reading in cm after computation
int dL=4; //distance pin indicator
int dR=6; //distance pin indicator

int pHArray[ArrayLenth];   //All arrays store the average value of the sensor feedback
int pHArrayIndex=0;       //All index vars store the index at which next reading is to be added
int turbArray[ArrayLenth];
int turbArrayIndex=0; 
int tempArray[ArrayLenth];
int tempArrayIndex=0;
int rainArray[ArrayLenth];
int rainArrayIndex=0; 
float rainVoltage,pHValue,turbVoltage,temp;  //Final readings should be stored


void setup(void)
{
  pinMode(dL, OUTPUT);
  digitalWrite(dL,LOW);
  pinMode(dR, OUTPUT);
  digitalWrite(dR,LOW);
  pinMode(trigPin1, OUTPUT); // Sets the trigPin as an Output
  pinMode(echoPin1, INPUT); // Sets the echoPin as an Input
  pinMode(trigPin2, OUTPUT); // Sets the trigPin as an Output
  pinMode(echoPin2, INPUT); // Sets the echoPin as an Input
  pinMode(LED,OUTPUT);
  digitalWrite(LED,LOW);
  Serial.begin(9600); 
  pinMode(PWM_PinRev, OUTPUT);
  attachInterrupt(pin3interruptRev, pinChangeISRRev, CHANGE); // call the function pinChangeISR each time the input changes state 
  sensors.begin();
 }
void loop(void)
{
  static unsigned long samplingTime = millis();
  static unsigned long printTime = millis();
  //After 20 ms get sensor data also send distance sensor readings 
  if(millis()-samplingTime > samplingInterval)
  {
     phRead();
     turbRead();
     tempRead();
     rainRead();
     samplingTime=millis();
  }
  //After 80 ms send all sensor readings
  if(millis() - printTime > printInterval)   //Every 800 milliseconds, print a numerical, convert the state of the LED indicator
  {
        d1();
        d2();
        Serial.print(distance);
        Serial.print(' ');
        Serial.println(distance2);
        Serial.print(temp);
        Serial.print(' ');
        Serial.print(pHValue);
        Serial.print(' ');
        Serial.print(turbVoltage);
        Serial.print(' ');
        Serial.println(rainVoltage);
        digitalWrite(LED,digitalRead(LED)^1);
        printTime=millis();
  }
  if(pulseLengthRev<1200)
  { 
    //Serial.println(pulseLengthRev);
    analogWrite(PWM_PinRev, 255);
  }
  else if(pulseLengthRev>1800)
  { 
    //Serial.println(pulseLengthRev);
    analogWrite(PWM_PinRev,0);
  }
  else
  { 
   // Serial.println(pulseLengthRev);
    analogWrite(PWM_PinRev, 255);
  }
     
    if(distance<70)
    { 
      //Serial.println(distance);
      digitalWrite(dL, HIGH);
    }
    else 
    { 
      //Serial.println(distance);
      digitalWrite(dL, LOW);
    }
  
    if(distance2<70)
    { 
      //Serial.println(distance2);
      digitalWrite(dR, HIGH);
    }
    else 
    { 
      //Serial.println(distance2);
      digitalWrite(dR, LOW);
    }
    if(distance2<50 && distance<50)
    {
        analogWrite(PWM_PinRev,0);
    }
      
}
/*
  *
  * Function Name: d1()
  * Input:    none
  * Output:     none
  * Logic:   Trigger the ultrasound sensor on left side, read the hight time of echo pin and accordingly compute distance using 
  *          Speed=distance/time
  * Example Call:   d1()
  *
  */ 
void d1() 
{
  // Clears the trigPin
  digitalWrite(trigPin1, LOW);
  delayMicroseconds(2);
  // Sets the trigPin on HIGH state for 10 micro seconds
  digitalWrite(trigPin1, HIGH);
  delayMicroseconds(10);
  digitalWrite(trigPin1, LOW);
  duration = pulseIn(echoPin1,HIGH);
  // Calculating the distance
  distance= duration/29/2;
  // Prints the distance on the Serial Monitor
}
/*
  *
  * Function Name: d2()
  * Input:    none
  * Output:     none
  * Logic:   Trigger the ultrasound sensor on right side, read the hight time of echo pin and accordingly compute distance using 
  *          Speed=distance/time
  * Example Call:   d2()
  *
  */ 
void d2() 
{
  // Clears the trigPin
  digitalWrite(trigPin2, LOW);
  delayMicroseconds(2);
  // Sets the trigPin on HIGH state for 10 micro seconds
  digitalWrite(trigPin2, HIGH);
  delayMicroseconds(10);
  digitalWrite(trigPin2, LOW);
  duration2 = pulseIn(echoPin2, HIGH);
  // Calculating the distance
  distance2= duration2/29/2;
  // Prints the distance on the Serial Monitor
}
/*
  *
  * Function Name: tempRead()
  * Input:    none
  * Output:     none
  * Logic:   Get temperature reading in the array and calculate its average 
  * Example Call:   tempRead()
  *
  */ 
void tempRead()
{
  sensors.requestTemperatures();
  tempArray[tempArrayIndex++]=sensors.getTempCByIndex(0)*100;
  if(tempArrayIndex==ArrayLenth)tempArrayIndex=0;
  temp = averagearray(tempArray, ArrayLenth);
  temp = temp/100; 
}
/*
  *
  * Function Name: turbRead()
  * Input:    none
  * Output:     none
  * Logic:   Get turbidity reading in the array and calculate its average. Convert ADC to voltage between 0 to 5
  * Example Call:   turbRead()
  *
  */ 
void turbRead()
{
  turbArray[turbArrayIndex++]=analogRead(turb);
  if(turbArrayIndex==ArrayLenth)turbArrayIndex=0;
  turbVoltage = averagearray(turbArray, ArrayLenth)*5.0/1024;
}
/*
  *
  * Function Name: rainRead()
  * Input:    none
  * Output:     none
  * Logic:   Get conductivity reading in the array and calculate its average. Convert ADC to voltage between 0 to 5
  * Example Call:   rainRead()
  *
  */ 
void rainRead()
{
  rainArray[rainArrayIndex++]=analogRead(rain);
  if(rainArrayIndex==ArrayLenth)rainArrayIndex=0;
  rainVoltage = averagearray(rainArray, ArrayLenth)*5.0/1024;
}
/*
  *
  * Function Name: phRead()
  * Input:    none
  * Output:     none
  * Logic:   Get ph reading in the array and calculate its average. Convert to ADC to voltage between 0 to 5
  * Example Call:   phRead()
  *
  */ 
void phRead()
{
   pHArray[pHArrayIndex++]=analogRead(pH);
   if(pHArrayIndex==ArrayLenth)pHArrayIndex=0;
   int voltage = averagearray(pHArray, ArrayLenth)*5.0/1024;
   pHValue = 3.5*voltage+Offset;
}
/*
  *
  * Function Name: averagearray()
  * Input:    array name, arraylength
  * Output:     none
  * Logic:   Get average of the entire array
  * Example Call:   averagearray(rainArray, ArrayLenth)
  *
  */ 
double averagearray(int* arr, int number)
{
  int i;
  int max,min;
  double avg;
  long amount=0;
  if(number<=0){
    Serial.println("Error number for the array to avraging!/n");
    return 0;
  }
  if(number<5){   
    //less than 5, calculated directly statistics
    for(i=0;i<number;i++){
      amount+=arr[i];
    }
    avg = amount/number;
    return avg;
  }else{
    if(arr[0]<arr[1]){
      min = arr[0];max=arr[1];
    }
    else{
      min=arr[1];max=arr[0];
    }
    for(i=2;i<number;i++){
      if(arr[i]<min){
        amount+=min;        //arr<min
        min=arr[i];
      }else {
        if(arr[i]>max){
          amount+=max;    //arr>max
          max=arr[i];
        }else{
          amount+=arr[i]; //min<=arr<=max
        }
      }//if
    }//for
    avg = (double)amount/(number-2);
  }//if
  return avg;
}


void pinChangeISRRev()  //ISR to get servo compatible pulse width and convert to mosfet compatible pwm 
{
  unsigned long timeNow = micros(); // record time
  if(digitalRead(RCinputPinRev)) // pulse now high
  {
    RCpulseLastChangeTime = timeNow; // save the time when the pulse went high
  }
  else // pulse now low
  {
    pulseLengthRev = int(timeNow - RCpulseLastChangeTime); // measure pulse length
    pulseLengthRev  = constrain(pulseLengthRev, MinPulseLength, MaxPulseLength); // correct bad readings
   // Serial.print(pulseLengthRev);
   // Serial.print("----->Rev");
   // Serial.println(map(pulseLengthRev, MinPulseLength, MaxPulseLength, 255, 0));
    
  }
}

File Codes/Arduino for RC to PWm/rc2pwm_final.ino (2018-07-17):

# /*
#   *
#   * Project Name:     Autonomous Water Rover
#   * Author List:      Chirag Shah
#   * Filename:         RCtoPWM.py
#   * Functions:        None Interrpt service routine is used.
#   * Global Variables:  MinPulseLength, MaxPulseLength, RCinputPinL, pin3interruptL,
#   *                    RCinputPinR, pin3interruptR, PWM_PinL, PWM_PinR, RCpulseLastChangeTime 
#   * Description: Converts RC output i.e. pulse between 1100 microseconds to 1900 microseconds \
#   *              from navio to normal PWM i.e. 0 to 255 (0V to 5V) 
# */
 
#define MinPulseLength 1100  // these are RC output obtained fromm Navio2
#define MaxPulseLength 1900

int RCinputPinL = 3;//physical pin mapping on uno
int pin3interruptL = 1; //ext interrupt 1
int RCinputPinR = 2; //physical pin mapping on uno
int pin3interruptR = 0; //ext interrupt 0

int PWM_PinL = 6; // PWM output pins
int PWM_PinR = 5;

int pulseLengthL=1100; 
int pulseLengthR =1100;

int lobstacle=10;
int robstacle=11;

unsigned long volatile RCpulseLastChangeTime = 0; //Timeout constant

void setup() {
  Serial.begin(9600);
  pinMode(lobstacle, INPUT);
  pinMode(robstacle, INPUT);  
  pinMode(PWM_PinL, OUTPUT);
  attachInterrupt(pin3interruptL, pinChangeISRL, CHANGE); // call the function pinChangeISR each time the input changes state
  pinMode(PWM_PinR, OUTPUT);
  attachInterrupt(pin3interruptR, pinChangeISRR, CHANGE); // call the function pinChangeISR each time the input changes state
}

void loop() {
  
  // signal drop safety check
  if(micros() - RCpulseLastChangeTime > 500000) // check if it has been more then 0.5s since last pulse was seen
  {
    analogWrite(PWM_PinL, 255); // set PWM outputs to 255
    analogWrite(PWM_PinR, 255);
  }
  if(pulseLengthR < pulseLengthL)
  {
    if(pulseLengthR==1100 && pulseLengthL==1900 )
    { 
        Serial.println("Hard Right");
        analogWrite(PWM_PinR, 255);
        analogWrite(PWM_PinL,10);
    }
    else
    {
        Serial.println("Soft Right");
        analogWrite(PWM_PinR,240);
        analogWrite(PWM_PinL,0);
           
    }
  }
  else if(pulseLengthL < pulseLengthR)
  {
    if(pulseLengthL==1100 && pulseLengthR==1900 )
    { 
        Serial.println("Hard Left");
        analogWrite(PWM_PinL, 255);
        analogWrite(PWM_PinR,10);
    }
    else
    {
        Serial.println("Soft Left");
        analogWrite(PWM_PinL, 250);
        analogWrite(PWM_PinR,10);
      
    }
  }
  else
  {
    if(pulseLengthL==1100 && pulseLengthR==1100 )
    { 
        Serial.println("Stop or reverse");
        analogWrite(PWM_PinL, 255);
        analogWrite(PWM_PinR,255);
    }
    else if(pulseLengthL==1900 && pulseLengthR==1900 )
    { 
        Serial.println("Forward");
        analogWrite(PWM_PinL, 0);
        analogWrite(PWM_PinR,60);
    }
  }
  if(digitalRead(lobstacle)==HIGH && digitalRead(robstacle)==HIGH)
  {
   // Serial.println("obstacle fwd");
   /* analogWrite(PWM_PinL, 255);
    analogWrite(PWM_PinR, 255);*/
  }
  else
  {
    if(digitalRead(lobstacle)==HIGH)
    {
       //Serial.println("obstacle left");
       /*
       analogWrite(PWM_PinL, 0);
       analogWrite(PWM_PinR, 255);*/
    }
    if(digitalRead(robstacle)==HIGH)
    {
       //Serial.println("obstacle right");
     /*  analogWrite(PWM_PinR, 0);
       analogWrite(PWM_PinL, 255);*/
    }
  }
  /*
    Serial.print(pulseLengthR);
    Serial.print("----->R");
    Serial.println(map(pulseLengthR, MinPulseLength, MaxPulseLength,255, 0));
    Serial.print(pulseLengthL);
    Serial.print("----->L");
    Serial.println(map(pulseLengthL, MinPulseLength, MaxPulseLength, 255, 0));*/
  delay(100); // wait 0.1s before checking again
}

void pinChangeISRL()  //ISR to get servo compatible pulse width and convert to mosfet compatible pwm 
{
  unsigned long timeNow = micros(); // record time
  if(digitalRead(RCinputPinL)) // pulse now high
  {
    RCpulseLastChangeTime = timeNow; // save the time when the pulse went high
  }
  else // pulse now low
  {
    pulseLengthL = int(timeNow - RCpulseLastChangeTime); // measure pulse length
    pulseLengthL  = constrain(pulseLengthL, MinPulseLength, MaxPulseLength); // correct bad readings
    
    //analogWrite(PWM_PinL, map(pulseLengthL, MinPulseLength, MaxPulseLength, 255, 0)); // update PWM signal
    //analogWrite(PWM_PinL, 255);
  }
}
void pinChangeISRR()    //ISR to get servo compatible pulse width and convert to mosfet compatible pwm 
{
  unsigned long timeNow = micros(); // record time
  
  if(digitalRead(RCinputPinR)) // pulse now high
  {
    RCpulseLastChangeTime = timeNow; // save the time when the pulse went high
  }
  else // pulse now low
  {
    pulseLengthR = int(timeNow - RCpulseLastChangeTime); // measure pulse length
    pulseLengthR  = constrain(pulseLengthR, MinPulseLength, MaxPulseLength); // correct bad readings
    //analogWrite(PWM_PinR, map(pulseLengthR, MinPulseLength, MaxPulseLength, 255,0)); // update PWM signal
    //analogWrite(PWM_PinR, 255);
  }
}

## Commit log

2018-07-17 Added arduino codes and media
2018-07-18 added process flow pdf in documents
2018-07-31 added cad drawing
    [14 Pin SMT.SLDPRT, 3 Pin Header 90 Degree.SLDPRT, Assem4.SLDASM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]
